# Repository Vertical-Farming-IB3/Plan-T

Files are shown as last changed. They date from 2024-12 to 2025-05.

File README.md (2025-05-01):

# Plan-T 🌱  

Plan-T is een vertical farming (VF) project met hydroponics, gericht op het duurzaam kweken van kruiden en groenten. De VF-installatie wordt grotendeels automatisch bestuurd en gemonitord, met ruimte voor menselijke input waar nodig — zoals bij controle, onderhoud en oogst (een vorm van mens-in-de-lus automatisering).

## Voor meer info:  
- [Team Plantenbak](./Plantenbak)  
- [Team Water](./Water)  
- [Team Licht](./Licht)
- [Team Power](./Power)  

Bezoek onze [website](https://vertical-farming-ib3.github.io/),
en zijn [repository](https://github.com/Vertical-Farming-IB3/vertical-farming-ib3.github.io/tree/main).

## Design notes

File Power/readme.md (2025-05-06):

Meer info [hier](https://vertical-farming-ib3.github.io/Power/).

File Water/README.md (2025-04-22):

# Water 💧

Onze groep bestaat uit:
- Charlotte Bert
- Kjell Naessens
- Niels Verhoeve
- Sander Haustraete

Wij verzorgen het watersysteem en alles dat daarmee te maken heeft! Onze PCB bestuurt de pompjes, mixers, UV-filter, ... en leest waarden in van hoogtesensoren, chemische probes, ...

Voor een volledige beschrijving van het watersysteem kan je terecht op [onze webpagina](https://vertical-farming-ib3.github.io/Water/).

Meer documentatie over de PCB vind je [hier](./PCB/), meer documentatie over de chemische probes [hier](./Chemische_probes.md) en meer documentatie over de vermogensmeting [hier](./Vermogensmeting.md).

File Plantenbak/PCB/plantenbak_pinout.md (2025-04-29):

## Onboard led: 
- GPIO2

## Fans:
- GPIO32 ( relais )
- 12V power

## NFC:
- I²C:
  - SDA op GPIO21
  - SCL op GPIO22
- VCC (3.3V)
- GND
  
## GY-SCD4:
- I²C: GPIO21 en 22
- VCC (3.3V)
- GND
  
## Capacitive soil moisture sensor
- GPIO34
- VCC (3.3V)
- GND
  
## Stroommeter
- GPIO35
- VCC (3.3V)
- GND

## BH1750 lichtmeter
- I²C: GPIO21 en 22
- VCC (3.3V)
- GND
- PULL DOWN

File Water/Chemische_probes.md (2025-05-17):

# Probes en hun belangrijkste kenmerken

## 232-01 Referentie-Elektrode Glazen Schaal Enkele Zoutbrug Referentiesonde Sensor:
Link: [232-01 Referentie-elektrode Glazen Schaal Enkele Zoutbrug Referentiesonde Sensor - Buy Reference Electrode Product on Alibaba.com](https://www.alibaba.com/product-detail/232-01-Reference-Electrode-Glass-Shell_60668853882.html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)

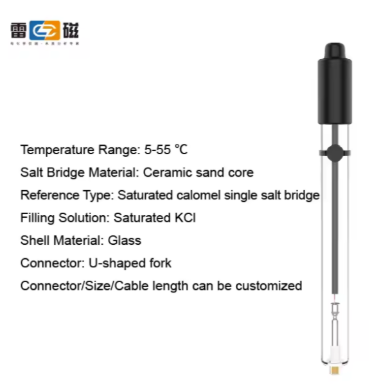
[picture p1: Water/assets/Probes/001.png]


### Belangrijkste kenmerken
#### Andere specificaties

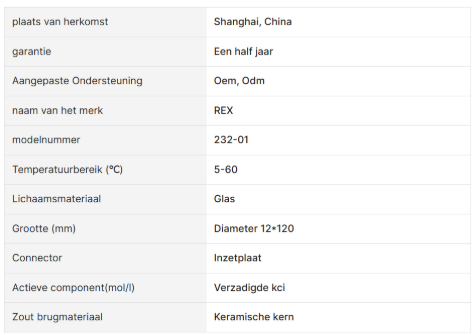
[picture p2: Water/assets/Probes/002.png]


## PCa-1-01 Calciumion Selectieve Sonde Isode Ca + Sensor
Link: [Pca-1-01 Calciumion Selectieve Sonde Isode Ca + Sensor - Buy Ion Selective Probe,Calcium Ion Selective Probe,Ion Selective Probe Product on Alibaba.com](https://www.alibaba.com/product-detail/PCa-1-01-Calcium-Ion-Selective_60659669573.html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)

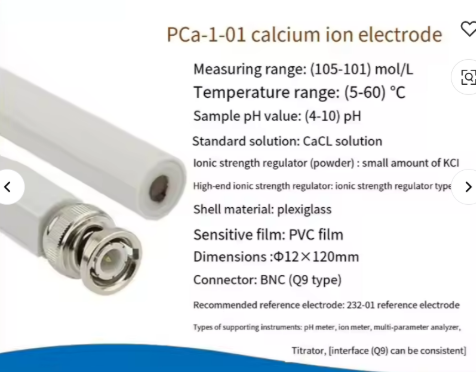
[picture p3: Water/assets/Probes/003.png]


### Belangrijkste kenmerken
#### Andere specificaties

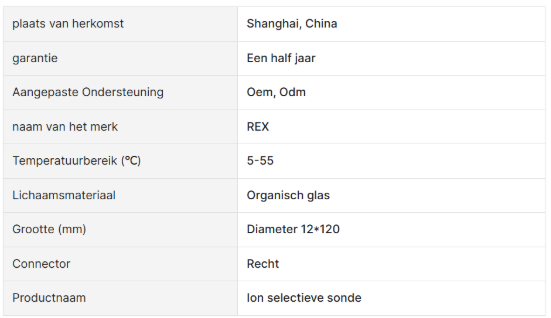
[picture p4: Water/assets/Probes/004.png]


## Ise K + Kalium Ion Selectieve Elektrode Bnc Connector Laboratorium En Gebruik Voor Waterkwaliteit Detectie Kalium Test Px Meter

Link: [Ise K + Kalium Ion Selectieve Elektrode Bnc Connector Laboratorium En Gebruik Voor Waterkwaliteit Detectie Kalium Test Px Meter - Buy Potassium ion Selective electrode Product on Alibaba.com](https://www.alibaba.com/product-detail/ISE-K-Potassium-Ion-Selective-Electrode_1600225607843.html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)

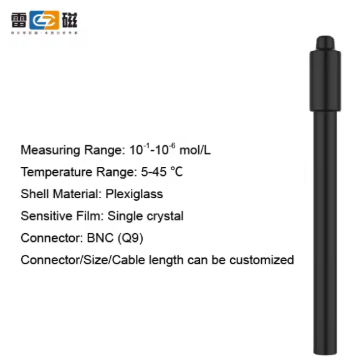
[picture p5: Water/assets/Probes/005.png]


### Belangrijkste kenmerken
#### Andere specificaties

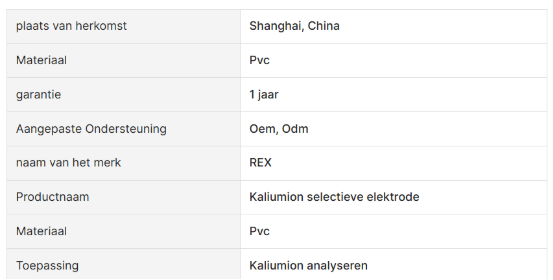
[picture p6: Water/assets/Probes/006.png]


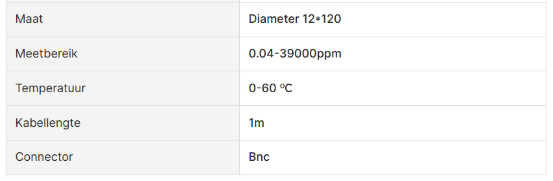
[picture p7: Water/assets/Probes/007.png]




## Nitraat Ion-Selectieve Elektrode No3-Ise Sonde Nitraat Ionen Verbindingen Algemene Water Test Bnc Connector

Link: [Nitraat Ion-selectieve Elektrode No3-ise Sonde Nitraat Ionen Verbindingen Algemene Water Test Bnc Connector - Buy Ion-selective Electrode no3- Ise Probe nitrate Ions Compounds Product on Alibaba.com](https://www.alibaba.com/product-detail/Nitrate-Ion-selective-Electrode-NO3-ISE_60817798149.html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)

### Belangrijkste kenmerken
#### Andere specificaties

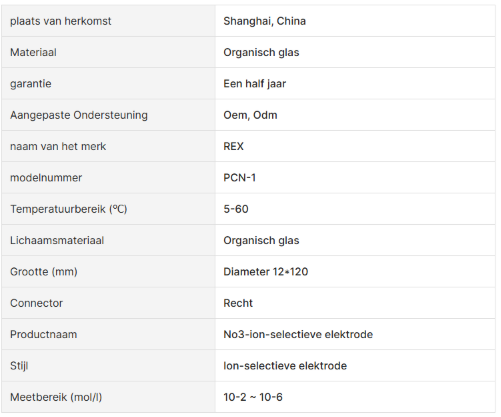
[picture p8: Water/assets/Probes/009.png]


Nauwkeurigheid: 0.01

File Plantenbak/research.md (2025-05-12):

---

## Research en vergelijking van sensoren

In deze sectie vergelijken we enkele van onze gekozen sensoren met alternatieve opties, op basis van nauwkeurigheid, prijs, beschikbaarheid, duurzaamheid en gebruiksgemak. Op basis van deze vergelijkingen motiveren we ook telkens onze keuze.

---

### Luchtsensor (GY-SCD40)

#### Vergelijking met alternatieven:

| Sensor | Parameters | Voeding | Interface | Nauwkeurigheid | Prijsindicatie | Opmerkingen |
|---|---|---|---|---|---|---|
| GY-SCD40 | CO₂, temperatuur, vochtigheid| 3.3V/5V | I²C | Hoog | Hoog | Compact, snel, nauwkeurig |
| MH-Z19B | CO₂ | 5V | UART | Matig | Gemiddeld | Alleen CO₂, trager, minder stabiel |
| CCS811 | eCO₂, TVOC | 3.3V | I²C | Laag tot gemiddeld | Laag | Indirecte CO₂, inferieur aan GY-SCD40 |

Zie onderstaande links voor verschillende sensoren:
- [GY-SCD40](https://www.tinytronics.nl/nl/sensoren/lucht/vochtigheid/gy-scd40-module-co2-luchtvochtigheid-en-temperatuursensor-i2c)
- [MH-Z19B](https://www.tinytronics.nl/nl/winsen-mh-z19b-co2-sensor-met-kabel)
- [CCS811](https://www.adafruit.com/product/3566)

#### Voordelen:
- Hoge nauwkeurigheid  
- Meet drie parameters tegelijk  
- Compact en efficiënt  

#### Nadelen:
- Duurder  
- Heeft enkele seconden opwarmtijd nodig  

**Keuze-motivatie:** Ondanks de hogere kostprijs is de SCD40 superieur door de combinatie van nauwkeurigheid, snelheid en veelzijdigheid. Dankzij hergebruik van een vorig project was er bovendien geen extra kost.

---

### NFC-lezer (PN532)

#### Vergelijking met alternatieven:

| Sensor | Interface | Bereik | Compatibiliteit | Prijsindicatie | Opmerkingen |
|---|---|---|---|---|---|
| PN532 | I²C/SPI/UART  | ~3 cm  | ISO/IEC 14443 A/B | Gemiddeld | Veelgebruikt, goede bibliotheekondersteuning |
| RC522 | SPI | ~2 cm  | ISO/IEC 14443 A | Laag | Korter bereik, minder robuust |
| MFRC630 | SPI/I²C | ~5 cm  | 14443 A/B + NFC Forum  | Hoog | Sneller en flexibeler, maar duurder en minder ingeburgerd |

Zie onderstaande links voor verschillende sensoren:
- [PN532](https://www.tinytronics.nl/en/communication-and-signals/wireless/rfid/rfid-nfc-kit-pn532-with-s50-card-and-s50-key-tag)
- [RC522](https://www.tinytronics.nl/nl/communicatie-en-signalen/draadloos/rfid/rfid-kit-mfrc522-s50-mifare-met-kaart-en-key-tag)
- [MFRC630](https://gr.mouser.com/c/semiconductors/wireless-rf-integrated-circuits/nfc-rfid-tags-transponders/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)
  
#### Voordelen:
- Brede ondersteuning, meerdere protocollen  
- Betrouwbaar en compatibel met ESP  
- Goede bibliotheekondersteuning  

#### Nadelen:
- Duurder dan RC522  
- Groter formaat  

**Keuze-motivatie:** De PN532 was beschikbaar op de campus en heeft een goede compatibiliteit met ESP32 en ESPHome. Daardoor was het de beste keuze voor snelle implementatie.

---

### Energiemonitoring (ACS712)

#### Vergelijking met alternatieven:

| Sensor | Meetprincipe | Meetbereik | Interface | Nauwkeurigheid | Prijsindicatie | Opmerkingen |
|---|---|---|---|---|---|---|
| ACS712 | Hall-effect | ±5A/20A/30A| Analoog | Gemiddeld | Laag | Beperkte resolutie, gevoelig aan ruis |
| INA219 | Shunt + ADC | Tot 3.2A | I²C | Hoog | Gemiddeld | Beter voor lage stromen, nauwkeuriger |
| SCT-013 | Transformatorspoel| 100A | Analoog | Laag tot gemiddeld | Laag | Alleen AC, extra burden resistor nodig |

Zie onderstaande links voor verschillende sensoren:
- [ACS712](https://www.tinytronics.nl/nl/sensoren/stroom-spanning/acs712-stroomsensor-module-20a)
- [INA219](https://www.tinytronics.nl/en/sensors/current-voltage/ina219-i2c-dc-current-and-voltage-meter-3.2a-module)
- [SCT-013](https://www.tinytronics.nl/nl/sensoren/stroom-spanning/ac-stroom-sensor-sct013-030-30a)

#### Voordelen:
- Simpel aan te sluiten (analoog)  
- Meet zowel AC als DC  
- Goedkoop en goed beschikbaar  

#### Nadelen:
- Gevoelig voor ruis  
- Lage resolutie, niet geschikt voor hele kleine stromen  

**Keuze-motivatie:** Omdat het systeem op lage stroom werkt, was de ACS712 accuraat genoeg voor onze noden. Bovendien had een teamlid deze sensor al thuis liggen, waardoor we dus budget konden sparen.

---

### Bodemsensor (Capacitive Soil Sensor v2)

#### Vergelijking met alternatieven:

| Sensor | Meetprincipe | Interface | Waterbestendig | Levensduur | Prijsindicatie | Opmerkingen |
|---|---|---|---|---|---|---|
| Capacitive Soil Sensor v2 | Capacitatief | Analoog | Spatwaterdicht | Gemiddeld  | Laag | Goede optie voor hydroponics |
| Resistive sensor (YL-69)  | Weerstandsmeting | Analoog | Nee | Laag | Zeer laag | Roest snel, onnauwkeurig |
| DFRobot SEN0193 | Capacitief digitaal  | UART/I2C/analog  | Waterdicht | Zeer goed  | Hoog (± €25–€35)| Professionele sensor, waterdicht, nauwkeurig |

Zie onderstaande links voor verschillende sensoren:
- [v2](https://www.tinytronics.nl/en/sensors/liquid/capacitive-soil-moisture-sensor-module-with-cable)
- [YL-69](https://nl.aliexpress.com/item/1005004305871722.html)
- [DFRobot SEN0193](https://be.farnell.com/dfrobot/sen0193/analog-capacitive-soil-moisture/dp/2946124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)

#### Voordelen:
- Capacitatieve meting is nauwkeuriger dan resistieve  
- Redelijk bestand tegen vocht  
- Werkt goed met ESPHome  

#### Nadelen:
- Niet volledig waterdicht  
- Niet geschikt voor diepe grondlagen  

**Keuze-motivatie:** Voor hydroponics volstaat een gemiddelde nauwkeurigheid. Deze sensor was reeds aanwezig in de klas en biedt een goed evenwicht tussen betrouwbaarheid en kost.

---

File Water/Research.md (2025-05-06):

# Research Water 
## Ontsmetten van mixreservoir 
Heel wat oplossingen voor het ontsmetten/zuiveren van het mixreservoir is duur en niet meteen beschikbaar.

Een zandfilter is een effectief systeem, maar moet regelmatig vervangen worden en brengt mogelijks hoge onderhoudskosten met zich mee.

Het gebruik van UV-C lampen, is effectief, onderhoudsvriendelijk en heeft een levensduur van 8000 uur wat goed is voor onze toepassing. Voor een effectieve werking mikken we op een golflengte tussen de 254 en 265 nm.

Voor de UV-C ontsmetting zijn er drie mogelijke plaatsingen besproken:

1. Boven alle reservoirs
  - Voordeel: Eén lamp kan meerdere reservoirs ontsmetten.
  - Nadeel: Grotere afstand en minder afscherming zorgen voor lagere effectiviteit en verhoogd risico op blootstelling van mens en dier aan schadelijk licht. Ook zou dit de levensduur van de tubes verlagen.

2. In het mengreservoir
  - Voordeel: Direct contact met het meest besmette water.
  - Nadeel: Enkel het mengreservoir wordt gezuiverd, en er is geen interne reflectie die de effectiviteit verhoogt.

3. Extern via tubes
  - Voordeel: Veelzijdig inzetbaar met pompsystemen en maakt gebruik van interne reflectie, wat zorgt voor een efficiëntere werking.
  - Nadeel: Meer externe hardware en coördinatie nodig, wat de kosten verhoogt.

Bij de keuze van de lamp houden we rekening met het benodigde vermogen, gebaseerd op het volume van de reservoirs en de concentratie voedingsstoffen. We streven naar een vermogen van ongeveer 10 watt.
Wij hebben gekozen voor optie 2, in het mengreservoir. Dit was het beste te implementeren in ons systeem. 

Ten slotte wensen we de lamp aan te sturen via een PCB met ESPHome, gekoppeld aan Home Assistant. Hiervoor kiezen we bewust voor een eenvoudige lamp zonder ingebouwde timer, die via een relais en schakelaar kan worden bestuurd.

De eerst bestelde UVC-lamp via AliExpress gaf problemen: deze ontplofte al na zeven minuten gebruik. Dit onderstreept het belang van kwaliteitsvolle componenten en betrouwbare leveranciers.

## Waterniveau Sensor

Er zijn verschillende opties voor waterniveau meting:

| Kenmerk | Waterniveau Sensor | DFRobot Contactloze Sensor | Ultrasone Sensor |
|---|---|---|---|
| Meetprincipe | Weerstand (direct contact) | Capacitief (contactloos) | Ultrasoon geluid |
| Contactloos? | Nee | Ja | Ja |
| Output | Analoog | Digitaal | Analoog |
| Meetbereik | Verschillende niveaus | Alleen "aan/uit" detectie | 2-450 cm |
| Nauwkeurigheid | Afhankelijk van vloeistofconductiviteit en corrosie | Betrouwbaar, maar geen niveau-indicatie | 3mm |
| Geschikt voor alle vloeistoffen? | Nee, alleen geleidende vloeistoffen | Ja | Ja |
| Corrosiegevoelig? | Ja | Nee | Nee |
| Prijs | Goedkoop | Duurder | 1-3 euro |
| Toepassing | Waterniveau meten | Vloeistofniveau detecteren zonder contact | Zeer nauwkeurig vloeistofniveau opmeten |

Zie onderstaande links voor verschillende sensoren:
- [Waterniveau Sensor](https://www.tinytronics.nl/nl/sensoren/vloeistof/waterniveau-sensor)
- [DFRobot Contactloze Sensor](https://www.tinytronics.nl/nl/sensoren/vloeistof/dfrobot-gravity-contactloze-vloeistofniveau-schakelaar-sensor)
- [Ultrasone Sensor](https://www.tinytronics.nl/en/sensors/distance/ultrasonic-sensor-hc-sr04)

We kozen voor de ultrasone sensor. De waterniveausensor was ook een goede keuze maar leek ons toch net niet helemaal geschikt. Beiden hebben nadelen en voordelen.

## Mixer
Er zijn verschillende opties voor watercirculatie:

- *Aquariumpomp*  
  - Voordelen: Sterke circulatie  
  - Nadelen: turbulentie veroorzaken en kan verstopt geraken  

- *Luchtpomp + luchtsteen*  
  - Voordelen: Zachte menging, weinig energieverbruik  
  - Nadelen: Trage menging en schuimvorming  

- *Mechanische mixer*  
  - Voordelen: Efficiënt mengen zonder veel turbulentie  
  - Nadelen: Mechanisch => onderhoud nodig  

We kozen voor een luchtpompje bij de reservoirs beneden. Dankzij een luchtsteen zal het water voldoende gecirculeerd worden.

Voor het reservoir kozen we een aquariumpompje. Dit heeft niet veel water nodig om een voldoende turbulente stroom te voorzien die het water mengt. Dit pompje sturen we aan op basis van de hoogte in dit bovenste reservoir.

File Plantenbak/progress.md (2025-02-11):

# Plantenbak
Teamleden:
  - Beau Forrez
  - Elias Neels
  - Wout Batselé
  - ...
  - ...

## To-do lijst
- [ ] Componentenlijst opstellen

## In Progress
- [ ] Componenten van vorig jaar testen en proberen te hergebruiken
- [ ] De server terug werkende krijgen

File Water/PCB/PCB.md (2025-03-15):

# PCB Watersysteem

In dit document sommen we de requirements op voor de PCB.

## Inputs
- Analoog (x3) voedingstoffen => via 1 ADC (ADS1115) met BNC connectoren voor de probes
- Analoog (x3) Ultrasone hoogtesensoren (HC-SR04)
- Digitaal (x3) eindeloopschakelaars

## Outputs
- Digitaal LED indicator waterniveau
- Digitaal LED indicator voedingsstofniveau
- Relais UV lamp (230V/100mA)
- Relais mixer pompje (3V/200mA) of (6V/200mA)
- Relais pompjes lade en reservoirs (4x) (12V/400mA)
- Relais luchtpomp (12V/220mA)

# Power inputs

12V DC / 3A

230V AC / 100mA

Dit wordt op de PCB door een buck converter (MP1584) van 12V naar 5V omgezet voor de relais. De 5V wordt verder omgevormd naar 3.3V door een LDO (AMS1117) voor de ESP32.
## Vermogen 12V
- 4x pompje van 400mA
- 1x luchtpomp 220mA
- 1x mixer pompje 100mA
- relais (200mA bij 5V) => 100mA
- Buck converter (1500mA bij 5V) => 800mA

Afgerond maakt dit 3000mA bij 12V \
=> P = 40W

# Pinout
Nummers: ESP32

A/B: IO expander \
IO expander is met I2C verbonden met de ESP32

### LEDs
Pin| Description
---|------------
2  | Onboard LED (IO2)
A7 | Water LED
B0 | Nutriënten LED

### Hoogtesensoren (ultrasoon)
Pin| Description
---|------------
26 | Trigger Hoogtesensor Nutr
25 | Echo Hoogtesensor Nutr
33 | Trigger Hoogtesensor Water
32 | Echo Hoogtesensor Water
14 | Trigger Hoogtesensor Mix
27 | Echo Hoogtesensor Mix

### Eindeloopschakelaars
Normaal open

Open = Hoog, Gesloten = Laag

 Pin | Description
-----|------------
 B1  | Schakelaar 1
 B2  | Schakelaar 2
 B3  | Schakelaar 3

### Relais

 Pin | Description
-----|------------
 A0  | Mixer
 A1  | UV lamp
 A2  | Luchtpomp
 A3  | Pomp 4
 A4  | Pomp 3
 A5  | Pomp 2
 A6  | Pomp 1

### Backup IO

Pin| Description
---|------------
B4 | B4
B5 | B5
B6 | B6
B7 | B7

### IO expander
I2C adres: 0X27

Het adres is herinstelbaar via JP1, JP2 en JP3 (verbind de jumpers voor een 0, ze zijn standaard 1): \
0b0100\<JP1>\<JP2>\<JP3>

### ADC en probes
I2C adres: 0x48 \
Verbind JP4 voor adres 0x49

Pin| Description
---|------------
A0 | Nutriënten 3
A1 | Nutriënten 2
A2 | Nutriënten 1
A3 | Referentie

Testpunten zijn aangeduid op de PCB

### I2C

Pin| Description
---|------------
17 | SCL
18 | SDA

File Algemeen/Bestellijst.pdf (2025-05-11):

Component | Status | Link | Aantal/module plantenbak | Aantal/module kast | Aantal in bezit | Totaal aantal | Totaal aantal te bestellen | Prijs/eenheid Kost | Prijs | Info | Totaal Watersysteem (Te bestellen) | Aantal modules kast:
WATERSYSTEEM | € 123,39 | 1
Waterpomp (12VDC) | In bezit | TinyTronics | 4 | 4 | 4 | € 6,00 | 24,00 € | 24,00 € | Aantal modules plantenbak per module kast:
Aquariumpomp (mengen) | In bezit | TinyTronics | 1 | 1 | 1 | € 4,00 | 4,00 € | 4,00 € | 2
Sensor ISE-2922 NO3- | In bezit | MTLAB | 1 | 1 | 1 | 0 | € 36,83 | 36,83 € | - € | Totaal aantal modules plantenbak:
Sensor ISE-2923 Ca2+ | In bezit | MTLAB | 1 | 1 | 1 | 0 | € 27,62 | 27,62 € | - € | 2
Sensor ISE-2920 K+ | In bezit | MTLAB | 1 | 1 | 1 | 0 | € 32,22 | 32,22 € | - €
ADC | In bezit | 1 | 1 | 1 | 0 | € 0,00 | - € | - € | op pcb
UV | Kapot | Aliexpress | 1 | 1 | 1 | € 10,43 | 10,43 € | 10,43 € | TOTALE KOST: | Excl verzending, excl xtra kosten, incl btw
Waterhoogte sensor: Ultrasoon | In bezit | TinyTronics | 3 | 3 | 3 | 0 | € 2,75 | 8,25 € | - €
QuickConnects water | In bezit | Aliexpress | 2 | 4 | 4 | 1 | € 0,97 | 3,88 € | 0,97 € | PU-8 voor 8 mm OD (1x 10 stuks bestellen) | TOTAAL TE BESTELLEN:
Waterslang (6mm ID-8mm OD) | In bezit | TinyTronics | 6 | 6 | 6 | € 1,50 | 9,00 € | 9,00 € | per meter (AAN 1 STUK BESTELLEN!) | € 766,62
Silicone kit | In bezit | Hubo | 1 | 1 | 1 | 0 | € 6,50 | 6,50 € | - €
Klemringen/Slangklemmen | In bezit | Aliexpress | 1 | 1 | 1 | € 2,33 | 2,33 € | 2,33 € | Per 10
Reservoir | In bezit | Vorig jaar | 4 | 4 | 4 | 0 | € 2,99 | 11,96 € | - €
Luchtsteen | In bezit | Aliexpress | 2 | 2 | 2 | € 0,97 | 1,94 € | 1,94 €
T stuk (luchtsteen) | In bezit | Aliexpress | 1 | 1 | 1 | € 0,97 | 0,97 € | 0,97 €
Luchtpomp | In bezit | TinyTronics | 2 | 2 | 2 | € 4,50 | 9,00 € | 9,00 €
Waterslang (3.5mm ID-Xmm OD) | In bezit | TinyTronics | 1 | 1 | 1 | € 2,00 | 2,00 € | 2,00 € | per meter, 3.5mm
Eindeloopschakelaars | In bezit | Hobbyelectronica | 3 | 3 | 3 | 0 | € 1,95 | 5,85 € | - €
PCBs | In bezit | PCBWay | 1 | 1 | 1 | € 4,39 | 4,39 € | 4,39 €
Relais 5V | In bezit | Mouser | 10 | 10 | 10 | € 1,47 | 14,70 € | 14,70 €
waterslang | In bezit | tinytronics | 1 | 1 | 1 | € 1,50 | € 1,50 | 1,50 €
PPF | In bezit | AliExpress | 5 | 5 | 5 | € 0,75 | € 3,80 | 3,80 €
PH- sensor + ADC | In bezit | AliExpress | 1 | 1 | € 4,52 | € 4,52 | 4,52 €
UV-C filter (nieuw) [14W - ordinary] | In bezit | AliExpress | 1 | 1 | € 29,84 | € 29,84 | 29,84 €
Componenten PCB
Footprint | Value | References | | | | | | | | Aanwezig op campus
C_0805_2012Metric_Pad1.18x1.45mm_HandSolder | 100n | C3, C4, C6, C7, C10, C11, C12, C13, C14 | 9 | 9 | 9 | 0 - | - | -
CP_Elec_6.3x3.9 | 100u | C1, C2 | 2 | 2 | 2 | 0 - | - | -
C_0805_2012Metric_Pad1.18x1.45mm_HandSolder | 10u | C5, C9 | 2 | 2 | 2 | 0 - | - | -
CP_EIA-3528-12_Kemet-T_Pad1.50x2.35mm_HandSolder | 22u | C8 | 1 yyyyy | 1 | 0 - | - | -
R_0805_2012Metric_Pad1.20x1.40mm_HandSolder | 10k | R2, R4, R5, R6, R7, R8, R9, R11, R13 | 9 | 9 | 9 | 0 - | - | -
R_0805_2012Metric_Pad1.20x1.40mm_HandSolder | 470 | R1, R3, R14, R15 | 4 | 4 | 4 | 0 - | - | -
R_0805_2012Metric_Pad1.20x1.40mm_HandSolder | 4.7k | R10, R12 | 2 | 2 | 2 | 0 - | - | -
D_0805_2012Metric_Pad1.15x1.40mm_HandSolder | 1N4148 | D4, D5, D6, D7, D8, D9, D10 | 7 | 7 | 7 | 0 - | - | -
LED_0805_2012Metric_Pad1.15x1.40mm_HandSolder | PWR | D1 | 1 | 1 | 1 | 0 - | - | -
LED_0805_2012Metric_Pad1.15x1.40mm_HandSolder | LED | D2 | 1 | 1 | 1 | 0 - | - | -
DIOM5226X290N | SK36A | D3 | 1 | 1 | 1 | 0 - | - | -
MP1584_Module | MP1584_Module | U1 | 1 | 1 | 1 | 0 - | - | -
ESP32-WROOM-32D | ESP32-WROOM-32D | U2 | 1 | 1 | 1 | 0 - | - | -
TSSOP-10_3x3mm_P0.5mm | ADS1115IDGS | U3 | 1 | 1 | 1 | 0 - | - | -
SOT-223-3_TabPin2 | AMS1117-3.3 | U4 | 1 | 1 | 1 | 0 - | - | -
SOIC-28W_7.5x17.9mm_P1.27mm | MCP23017_SO | U5 | 1 | 1 | 1 | 0 - | - | -
Wurth_Tactile_Switch_SPST-NO_434111043826 | EN | SW1 | 1 | 1 | 1 | 0 - | - | -
Wurth_Tactile_Switch_SPST-NO_434111043826 | BOOT | SW2 | 1 | 1 | 1 | 0 - | - | -
AHQSS105DM2FA0G | AHQSS105DM2FA0G | K1, K2, K3, K4, K5, K6, K7 | 7 | 7 | 7 | 0 - | - | -
SOT-23 | BSS138 | Q1, Q2, Q3, Q4, Q5, Q6, Q7 | 7 | 7 | 7 | 0 - | - | -
MountingHole_3.2mm_M3_Pad_TopBottom | MountingHole_Pad | H1, H2, H3, H4 | 4 | 4 | 4 | 0 - | - | -
SolderJumper-2_P1.3mm_Open_RoundedPad1.0x1.5mm | SolderJumper_2_Open | JP1, JP2, JP3, JP4 | 4 | 4 | 4 | 0 - | - | -
TestPoint_Pad_D2.0mm | TestPoint | TP1, TP2, TP3, TP4 | 4 | 4 | 4 | 0 - | - | -
PinHeader_1x04_P2.54mm_Vertical | Height Water | J1 | 1 | 1 | 1 | 0 - | - | -
PinHeader_1x04_P2.54mm_Vertical | Height Nutrients | J2 | 1 | 1 | 1 | 0 - | - | -
PinHeader_1x04_P2.54mm_Vertical | Height Mixer | J3 | 1 | 1 | 1 | 0 - | - | -
PinHeader_1x02_P2.54mm_Vertical | TestPins | J4 | 1 | 1 | 1 | 0 - | - | -
TerminalBlock_Phoenix_PT-1,5-2-5.0-H_1x02_P5.00mm_Horizontal | 12V ingang | J5 | 1 | 1 | 1 | 0 - | - | -
TerminalBlock_Phoenix_PT-1,5-2-5.0-H_1x02_P5.00mm_Horizontal | Pomp1 | J6 | 1 | 1 | 1 | 0 - | - | -
PinHeader_1x04_P2.54mm_Vertical | TTL Connector | J7 | 1 | 1 | 1 | 0 - | - | -
PinHeader_1x03_P2.54mm_Vertical | Endstop UV | J8 | 1 | 1 | 1 | 0 - | - | -
PinHeader_1x03_P2.54mm_Vertical | Endstop Lade1 | J9 | 1 | 1 | 1 | 0 - | - | -
BNC_Amphenol_B6252HB-NPP3G-50_Horizontal | ReferentieProbe | J10 | 1 | 1 | 1 | 0 - | - | -
PinHeader_1x03_P2.54mm_Vertical | Endstop Lade0 | J11 | 1 | 1 | 1 | 0 - | - | -
TerminalBlock_Phoenix_PT-1,5-2-5.0-H_1x02_P5.00mm_Horizontal | Pomp2 | J12 | 1 | 1 | 1 | 0 - | - | -
PinHeader_1x02_P2.54mm_Vertical | LED Water Level | J13 | 1 | 1 | 1 | 0 - | - | -
PinHeader_1x02_P2.54mm_Vertical | LED Nutrient Level | J14 | 1 | 1 | 1 | 0 - | - | -
BNC_Amphenol_B6252HB-NPP3G-50_Horizontal | Voedingsstoffen 1 | J15 | 1 | 1 | 1 | 0 - | - | -
TerminalBlock_Phoenix_PT-1,5-2-5.0-H_1x02_P5.00mm_Horizontal | Pomp3 | J16 | 1 | 1 | 1 | 0 - | - | -
TerminalBlock_Phoenix_PT-1,5-2-5.0-H_1x02_P5.00mm_Horizontal | Pomp4 | J17 | 1 | 1 | 1 | 0 - | - | -
PinHeader_1x06_P2.54mm_Vertical | Backup GPIO | J18 | 1 | 1 | 1 | 0 - | - | -
BNC_Amphenol_B6252HB-NPP3G-50_Horizontal | Voedingsstoffen 2 | J19 | 1 | 1 | 1 | 0 - | - | -
TerminalBlock_Phoenix_PT-1,5-2-5.0-H_1x02_P5.00mm_Horizontal | Luchtpomp | J20 | 1 | 1 | 1 | 0 - | - | -
BNC_Amphenol_B6252HB-NPP3G-50_Horizontal | Voedingsstoffen 3 | J21 | 1 | 1 | 1 | 0 - | - | -
TerminalBlock_Phoenix_PT-1,5-2-5.0-H_1x02_P5.00mm_Horizontal | Mixer | J22 | 1 | 1 | 1 | 0 - | - | -
TerminalBlock_Phoenix_PT-1,5-2-5.0-H_1x02_P5.00mm_Horizontal | 230V | J23 | 1 | 1 | 1 | 0 - | - | -
TerminalBlock_Phoenix_PT-1,5-2-5.0-H_1x02_P5.00mm_Horizontal | UV | J24 | 1 | 1 | 1 | 0 - | - | -
PLANTENBAK | | | | | | | | | | | Totaal Plantenbak (Te bestellen)
Capacitive soil moisture sensor | In bezit | 1 | 2 | 2 | 2 | € 87,43
GY-SCD40 module | In bezit | 1 | 2 | 2 | 2
NFC-reader PN532 | In bezit | 1 | 2 | 2 | 2
NFC-tags | In bezit | 1 | 2 | 2 | 2
Nieuwe PCB's | In bezit | PCBWay | 1 | 2 | 2 | 2 | 4,39 €
BH1750 lichtsensor | In bezit | Hobbyelectronica | 1 | 2 | 2 | 2 | € 2,25 | € 4,50 | 4,50 €
CH340C | In bezit | AliExpress | 1 | 2 | 10 | 10 | € 0,41 | € 4,05 | 4,05 €
ESP-WROOM-32 | In bezit
Ventilatoren (12V) | In bezit | 2 | 4 | 4 | 4
Relais SR5 | In bezit | Digikey | 1 | 2 | 2 | 2 | € 1,13 | € 2,26 | 2,26 €
MP1584 | In bezit | TinyTronics | 1 | 2 | 2 | 2 | € 1,50 | € 3,00 | 3,00 €
Dupont kabels | In bezit | 4 | 4 | € 2,00 | € 8,00 | 8,00 €
5V relais | In bezit | Tinytronics | 2 | 2 | € 2,50 | € 5,00 | 5,00 €
rockwol aliexpress | In bezit | AliExpress | 1 | 1 | € 4,65 | € 4,65 | 4,65 € | 100 stuks per batch
potjes voor plantjes: NO.40 white | In bezit | AliExpress | 2 | 2 | € 3,28 | € 3,28 | 6,56 € | NO.50 white (15 stuk per batch)
witte verf | In bezit | Action | 1 | 1 | € 7,99 | € 7,99 | 7,99 €
verfborstel en verfbak | In bezit | action | 1 | 1 | € 1,84 | € 1,84 | 1,84 €
kokosvezel potgrond | In bezit | Action | 3 | 3 | € 1,17 | € 3,51 | 3,51 €
plantenvoeding | In bezit | Action | 2 | 2 | € 1,79 | € 3,58 | 3,58 €
bloempotjes | In bezit | action | 2 | 2 | € 1,11 | € 2,22 | 2,22 €
hydrokorrels | In bezit | Action | 1 | 1 | € 2,37 | € 2,37 | 2,37 €
Glasbokalen | In bezit | Action | 9 | 9 | € 0,89 | € 8,01 | 8,01 €
Kitlijm voor bakken | In bezit | Gamma | 1 | 1 | € 11,00 | € 11,00 | 11,00 €
Regentonkraan voor bakken | In bezit | EuroShop | 1 | 1 | € 4,50 | € 4,50 | 4,50 €
Componenten PCB
Footprint | Value | References | | | | | | | | Aanwezig op campus
Capacitor_SMD:C_0805_2012Metric_Pad1.18x1.45mm_HandSolder | 10u | C1 C7 C8 C9 C12 | 5 | 10 | 10 | 10 | 0
Capacitor_SMD:C_0805_2012Metric_Pad1.18x1.45mm_HandSolder | 100n | C2 C3 C10 C11 | 4 | 8 | 8 | 8 | 0
Capacitor_SMD:C_0805_2012Metric_Pad1.18x1.45mm_HandSolder | 1u | C5 | 1 | 2 | 2 | 2 | 0
Capacitor_SMD:C_0805_2012Metric_Pad1.18x1.45mm_HandSolder | 100u | C6 | 1 | 2 | 2 | 2 | 0
Diode_SMD:D_SOD-323_HandSoldering | D_Schottky | D1 D4 | 2 | 4 | 4 | 4 | 0
LED_SMD:LED_0805_2012Metric_Pad1.15x1.40mm_HandSolder | LED | D2 D3 | 2 | 4 | 4 | 4 | 0
Diode_SMD:D_SOD-123 | 1N4148W | D5 | 1 | 2 | 2 | 2 | 0
Connector_PinHeader_2.54mm:PinHeader_1x02_P2.54mm_Vertical | Conn_01x02 | J2 J3 | 2 | 4 | 4 | 4 | 0
Connector_PinHeader_2.54mm:PinHeader_1x04_P2.54mm_Vertical | Conn_01x04 | J4 J8 J14 J15 | 4 | 8 | 8 | 8 | 0
Connector_PinHeader_2.54mm:PinHeader_1x05_P2.54mm_Vertical | Conn_01x05 | J5 J7 | 2 | 4 | 4 | 4 | 0
Connector_PinHeader_2.54mm:PinHeader_1x10_P2.54mm_Vertical | Conn_01x10 | J6 J10 | 2 | 4 | 4 | 4 | 0
TerminalBlock_Phoenix:TerminalBlock_Phoenix_MKDS-1 | Screw_Terminal_01x02 | J9 J11 | 2 | 4 | 4 | 4 | 0
Connector_PinHeader_2.54mm:PinHeader_2x02_P2.54mm_Vertical | Conn_02x02_Counter_Clockwise J12 | 1 | 2 | 2 | 2 | 0
Connector_PinHeader_2.54mm:PinHeader_1x03_P2.54mm_Vertical | Conn_01x03 | J13 | 1 | 2 | 2 | 2 | 0
Package_TO_SOT_SMD:SOT-23 | BSS138 | Q1 Q2 Q3 Q4 Q5 | 5 | 10 | 10 | 10 | 0
Resistor_SMD:R_0805_2012Metric_Pad1.20x1.40mm_HandSolder | 4K7 | R1 R2 R5 R6 | 4 | 8 | 8 | 8 | 0
Resistor_SMD:R_0805_2012Metric_Pad1.20x1.40mm_HandSolder | 1M | R3 | 1 | 2 | 2 | 2 | 0
Resistor_SMD:R_0805_2012Metric_Pad1.20x1.40mm_HandSolder | 10K | R4 R7 R8 R9 R10 R11 R12 R14 R16 | 9 | 18 | 18 | 18 | 0
Resistor_SMD:R_0805_2012Metric_Pad1.20x1.40mm_HandSolder | 1K | R13 R15 R17 | 3 | 6 | 6 | 6 | 0
434111043826:434111043826 | SW_Push | SW1 SW2 | 2 | 4 | 4 | 4 | 0
Watersysteem_Footprints_Library:MP1584_Module | MP1584_Module | U1 | 1 | 2 | 2 | 2 | 0
Package_TO_SOT_SMD:SOT-223-3_TabPin2 | AMS1117-3.3 | U2 | 1 | 2 | 2 | 2 | 0
RF_Module:ESP32-WROOM-32E | ESP32-WROOM-32E | U4 | 1 | 2 | 2 | 2 | 0
Verlichting en power | nt | | | | | | | | | | Totaal Licht (Te bestellen)
Houten plaat | In bezit | 1 | 2 | 2 | 2 | 0 | € 0,00 | € 0,00 | - € | € 243,21
Main connector | In bezit | Mouser | 0 | 1 | 1 | 1 | € 13,35 | € 13,35 | 13,35 €
Netsnoer | In bezit | 0 | 1 | 2 | 1 | 0 - | - | -
Connectoren kast | In bezit | tinytronics | 1 | 4 | 4 | 4 | € 2,00 | € 8,00 | 8,00 €
conectoren led pcb's | In bezit | tinytronics | 6 | 9 | 9 | 9 | € 0,60 | € 5,40 | 5,40 €
12v 3A supply voor water en planten | In bezit | Mouser | 0 | 1 | 1 | 1 | € 16,52 | € 16,52 | 16,52 €
24v 4.2 A supply voor verlichting | In bezit | Mouser | 0 | 1 | 1 | 1 | € 23,81 | € 23,81 | 23,81 €
Fuse voor main connector | In bezit | Mouser | 1 | 1 | 1 | 1 | € 5,22 | € 5,22 | 5,22 €
Knop | In bezit | Mouser | 1 | 2 | 2 | 2 | € 0,30 | € 0,60 | 0,60 €
Stencils | In bezit | 2 | 2 | € 13,23 | € 13,23 | 26,46 €
Thermische Lijm | In bezit | RS | 1 | 1 | € 10,25 | € 10,25 | € 10,25

Componenten LED-PCB
Led PCB | In bezit | PCBWay | 5 | 10 | 10 | 10 | € 0,44 | € 4,41 | 4,41 € | 15 ipv 10?
Ver rode leds | In bezit | Ver rode leds Mouser | 20 | 40 | 40 | 40 | € 0,28 | € 11,36 | 11,36 €
Rode leds | In bezit | Rode leds Mouser | 30 | 60 | 60 | 60 | € 0,27 | € 15,96 | 15,96 €
Blauwe leds | In bezit | Blauwe leds Mouser | 20 | 40 | 40 | 40 | € 0,21 | € 8,44 | 8,44 €
Heatsink LED-PCB | In bezit | RS | 1 | 1 | 1 | 1 | € 37,94 | € 37,94 | 37,94 €
Thermal Pad LED-PCB | In bezit | RS | 1 | 2 | 2 | 2 | € 21,81 | € 43,62 | 43,62 €
Componenten Driver-PCB
Driver PCB | In bezit | PCBWay | 5 | 10 | 10 | 10 | € 0,44 | € 4,41 | 4,41 €
LDO voor ESP | In bezit | Mouser | 0 | 1 | 1 | 1 | € 0,71 | € 0,71 | 0,71 €
ESP-WROOM-32 | In bezit | 1 | 2 | 2 | 2 | 0 | € 0,00 | € 0,00 | - €
Connector driver pcb | In bezit | tinytronics | 1 | 2 | 2 | 2 | € 0,30 | € 0,60 | 0,60 €
Driver IC | In bezit | Mouser | 5 | 10 | 10 | 10 | € 0,48 | € 4,84 | 4,84 €
LDO voor ESP | In bezit | Mouser | 1 | 2 | 2 | 2 | € 0,66 | € 1,31 | 1,31 €
Driver Heatsink | In bezit | | | | | | | | | Nog aanvullen

Componenten per Driver-PCB
Footprint | Value | References
CAPC2013X95X50LL10T25 | Capacitor 100 nF +/-10% 50 V 0805C1, C2, C3, C4, C5 | 5
AL1793AFE13 | IC1_1, IC1_2, IC1_3 | 3
ESPWROOM32D | IC2 | 1
UA78M33IKVURG3 | Voltage Regulator | IC3 | 1
2828346 | Connector | J1_1, J1_2, J1_3 | 3
282834-2_1 | Connector | J2 | 1
61300411121 | Pin Header | P1 | 1
Resistors | Resistors | R1_1, R1_2, R1_3, R2_1, R2_2, R2_3, R3_1, R3_2, R3_3, R4_1, R4_2, R4_3, R5_1, R5_2, R5_3, R6_1, R6_2, R6_3, R7_1, R7_2, R7_3, R8 | 22
FSM4JSMATR | Micro Miniature Push Button Switch FSM JSM, 50 mA, -35 to 85 degC, 4-Pin SMD, RoHS, Tape and Reel SW1 | 1
Componenten per LED-PCB
Footprint | Value | References
282834-6 | Connector | J0, J1 | 2
JE2835ARY-N-0002A0000-N0000001 | LED | B0, B1, B2 | 3
JE2835AFR-N-0001A0000-N0000001 | LED | FR0, FR1, FR2, FR3 | 4
JE2835AHR-N-0001A0000-N0000001 | LED | R0, R1, R2, R3, R4 | 5
KAST | | | | | | | | | | | Totaal Buitenkast (Te bestellen)
€ 312,59
Hout binnenkast (schatting) | Resthout
| afmetingen | aantal
2000x600x18 | 4
Oude laden | 6

Gextrudeerde aluminium profielen
| afmetingen | aantal
2200x90x45 | 4
640x90x45 | 4
550x90x45 | 4
Wieltjes
Draaiend | 2
Vast | 2

Houtschroeven

DEUR
lengte | aantal
deurkader (sectie 18 mm x 60mm)
2,294 | 2 | 4,588
2,33 | 2 | 4,66
0,732 | 2 | 1,464
2,194 | 1 | 2,194
0,56 | 1 | 0,56
0,736 | 1 | 0,736
Totaal: | lengte | 14,202 m
breedte | 0,06 m
opp | 0,85212 m^2 | € 95,79 eenheidsprijs/m2 eurabo
prijs | € 81,62
aantal
klepscharnieren | 14 | € 4,69 | € 65,66 | Scharnieren

MMLAB plaat 840 x 1200 x 6
| 2 | € 42,12 | € 84,24

ZIJKANTEN: fineerplaten op kaders
breedte | 0,73 m
hoogte | 2,33 m
aantal | 2
opp | 3,4018 m2 | € 23,83 eenheidsprijs CRAS Merelbeke
| prijs | | € 81,06
Blachon | | | | Blanchon

gerecupereerd

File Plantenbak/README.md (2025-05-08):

# Plantenbak 🌱

Onze groep bestaat uit:
- Beau Forrez
- Elias Neels
- Wout Batsele
- Sander De Stercke
- Wouter Fouquet

Meer info vindt u [hier](https://vertical-farming-ib3.github.io/Plantenbak/).

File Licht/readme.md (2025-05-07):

Het team bestaat uit:
- Daan Vercammen
- Andres Bosman
- Syme Vandenbosch
- Arne Van der Stede
- Cas Truyers
- Stijn Verhaeghe

Meer info [hier](https://vertical-farming-ib3.github.io/Licht/).

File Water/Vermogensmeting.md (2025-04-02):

### Stroommeting - Berekende Resultaten

We meten het vermogen door de stroom te meten en deze te vermenigvuldigen met de spanning. De stroom wordt gemeten door een ACS712 sensor. Deze meet aan de hand van het Hall-effect een stroom tot 5 A. Wij zullen echter nooit een stroom van 3 A overtreffen (in uiterste gevallen). Om de analoge uitgangsspanning van deze sensor te beperken tot het bereik van de ADC van de ESP maken we gebruik van een spanningsdeler. Deze bestaat uit een 100k en een 10k weerstand.

We legden verschillende lasten aan om tot onderstaande gegevens te komen.

| Stroom (A) | Gemeten Spanning (V) | Voorspelde Stroom (A) | Afwijking (%) | Vermogen (W) | Opmerkingen |
|---|---|---|---|---|---|
| 0.032 | 2.34 | 0.047 | -46.88 | 0.56 | Grote afwijking bij lage stroom |
| 0.252 | 2.37 | 0.231 | 8.33 | 2.77 | |
| 0.56 | 2.43 | 0.598 | -6.79 | 7.18 | |
| 0.96 | 2.50 | 1.026 | -6.88 | 12.31 | |
| 1.06 | 2.51 | 1.088 | -2.64 | 13.06 | |
| 1.28 | 2.54 | 1.271 | 0.70 | 15.25 | Meest nauwkeurig |
| 1.66 | 2.60 | 1.638 | 1.33 | 19.66 | |
| 1.86 | 2.63 | 1.821 | 2.10 | 21.85 | |
| 2.06 | 2.67 | 2.066 | -0.29 | 24.79 | |

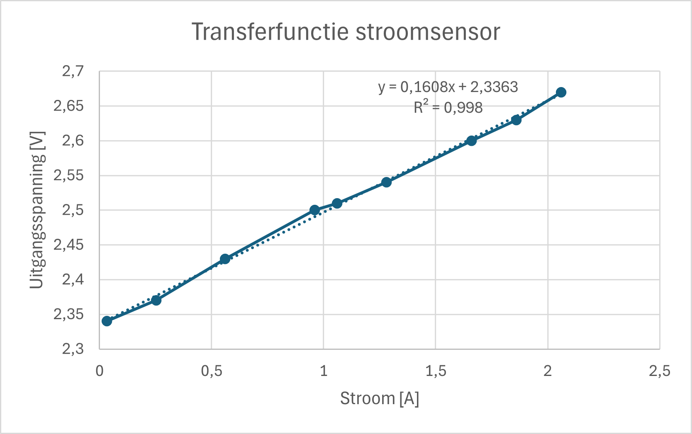
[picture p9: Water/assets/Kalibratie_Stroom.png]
Stroommeting Grafiek
  

**Berekeningsmethoden:**
- **Voorspelde Stroom (A):**  
  `(Gemeten Spanning - 2.3323) / 0.1634`  

- **Afwijking (%):**  
  `(1 - (Voorspelde Stroom / Gemeten Stroom)) × 100`  

- **Vermogen (W):**  
  `Voorspelde Stroom × 12V`  
  Ideaal meten we ook analoog de ingangsspanning op (met een spanningsdeler). We veronderstellen nu echter een constante ingangsspanningvan 12V.

**Conclusies:**
1. Het model is het meest nauwkeurig bij hogere stromgen.
2. Grote afwijkingen treden op bij lage stromen (-46.88% bij 0.032A)
3. Vermogensberekening is consistent gebaseerd op de voorspelde stroom

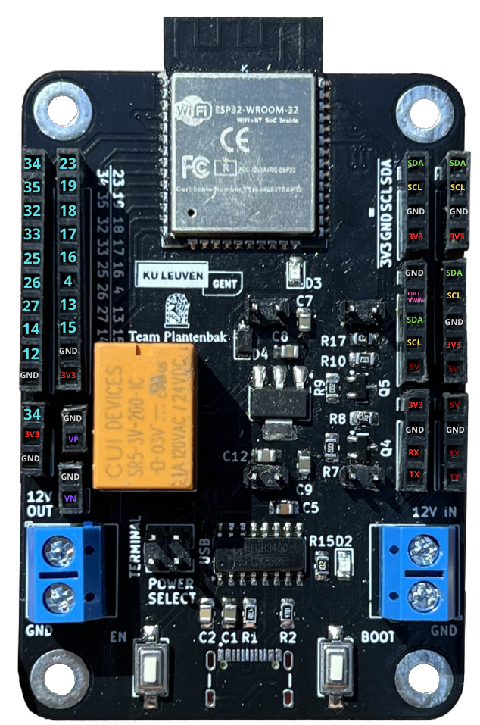
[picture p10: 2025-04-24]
Plantenbak/PCB/pinout.png

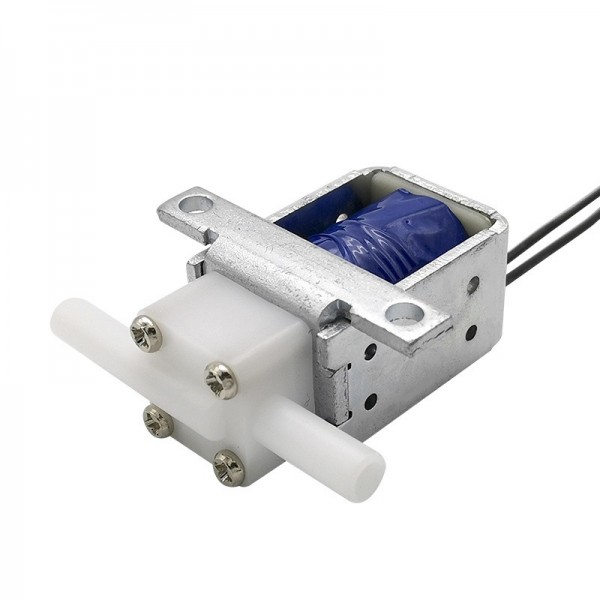
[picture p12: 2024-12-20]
Water/assets/Magneetventiel.jpg

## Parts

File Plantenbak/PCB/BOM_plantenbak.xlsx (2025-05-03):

Footprint | Value | References
Capacitor_SMD:C_0805_2012Metric_Pad1.18x1.45mm_HandSolder | 10u | C1 C7 C8 C9 C12
Capacitor_SMD:C_0805_2012Metric_Pad1.18x1.45mm_HandSolder | 100n | C2 C3 C10 C11
Capacitor_SMD:C_0805_2012Metric_Pad1.18x1.45mm_HandSolder | 1u | C5
Capacitor_SMD:C_0805_2012Metric_Pad1.18x1.45mm_HandSolder | 100u | C6
Diode_SMD:D_SOD-323_HandSoldering | D_Schottky | D1 D4
LED_SMD:LED_0805_2012Metric_Pad1.15x1.40mm_HandSolder | LED | D2 D3
Diode_SMD:D_SOD-123 | 1N4148W | D5
Connector_PinHeader_2.54mm:PinHeader_1x02_P2.54mm_Vertical | Conn_01x02 | J2 J3
Connector_PinHeader_2.54mm:PinHeader_1x04_P2.54mm_Vertical | Conn_01x04 | J4 J8 J14 J15
Connector_PinHeader_2.54mm:PinHeader_1x05_P2.54mm_Vertical | Conn_01x05 | J5 J7
Connector_PinHeader_2.54mm:PinHeader_1x10_P2.54mm_Vertical | Conn_01x10 | J6 J10
TerminalBlock_Phoenix:TerminalBlock_Phoenix_MKDS-1 | Screw_Terminal_01x02 | J9 J11
Connector_PinHeader_2.54mm:PinHeader_2x02_P2.54mm_Vertical | Conn_02x02_Counter_Clockwise | J12
Connector_PinHeader_2.54mm:PinHeader_1x03_P2.54mm_Vertical | Conn_01x03 | J13
Package_TO_SOT_SMD:SOT-23 | BSS138 | Q1 Q2 Q3 Q4 Q5
Resistor_SMD:R_0805_2012Metric_Pad1.20x1.40mm_HandSolder | 4K7 | R1 R2 R5 R6
Resistor_SMD:R_0805_2012Metric_Pad1.20x1.40mm_HandSolder | 1M | R3
Resistor_SMD:R_0805_2012Metric_Pad1.20x1.40mm_HandSolder | 10K | R4 R7 R8 R9 R10 R11 R12 R14 R16
Resistor_SMD:R_0805_2012Metric_Pad1.20x1.40mm_HandSolder | 1K | R13 R15 R17
434111043826:434111043826 | SW_Push | SW1 SW2
Watersysteem_Footprints_Library:MP1584_Module | MP1584_Module | U1
Package_TO_SOT_SMD:SOT-223-3_TabPin2 | AMS1117-3.3 | U2
RF_Module:ESP32-WROOM-32E | ESP32-WROOM-32E | U4

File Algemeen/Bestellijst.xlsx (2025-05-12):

Component | Status | Link | Aantal/module plantenbak | Aantal/module kast | Aantal in bezit | Totaal aantal | Totaal aantal te bestellen | Prijs/eenheid | Kost | Prijs | Info | Totaal Watersysteem (Te bestellen) | Aantal modules kast:
WATERSYSTEEM |  |  |  |  |  |  |  |  |  |  |  | €123.39 | 1
Waterpomp (12VDC) | In bezit | TinyTronics (https://www.tinytronics.nl/nl/mechanica-en-actuatoren/motoren/pompen/waterpomp-12v) |  | 4 |  | 4 | 4 | €6.00 | €24.00 | €24.00 |  |  | Aantal modules plantenbak per module kast:
Aquariumpomp (mengen) | In bezit | TinyTronics (https://www.tinytronics.nl/nl/mechanica-en-actuatoren/motoren/pompen/onderwaterpomp-horizontaal-3-6v) |  | 1 |  | 1 | 1 | €4.00 | €4.00 | €4.00 |  |  | 2
Sensor ISE-2922 NO3- | In bezit | MTLAB (http://www.measureteq.com/electrode-and-sensor/ion-selective-electrode/ise-2922-no3-nitrate-ion-selective-electrode.html) |  | 1 | 1 | 1 | 0 | €36.83 | €36.83 | €0.00 |  |  | Totaal aantal modules plantenbak:
Sensor ISE-2923 Ca2+ | In bezit | MTLAB (http://www.measureteq.com/electrode-and-sensor/ion-selective-electrode/ise-2923-calcium-ion-selective-electrode-ise.html) |  | 1 | 1 | 1 | 0 | €27.62 | €27.62 | €0.00 |  |  | 2
Sensor ISE-2920 K+ | In bezit | MTLAB (http://www.measureteq.com/electrode-and-sensor/ion-selective-electrode/ise-2920-potassium-ion-selective-electrode.html) |  | 1 | 1 | 1 | 0 | €32.22 | €32.22 | €0.00
ADC | In bezit |  |  | 1 | 1 | 1 | 0 | €0.00 | €0.00 | €0.00 | op pcb
UV | Kapot | Aliexpress (https://nl.aliexpress.com/item/1005004493335123.html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) |  | 1 |  | 1 | 1 | €10.43 | €10.43 | €10.43 |  |  | TOTAAL TE BESTELLEN: | Excl verzending, excl xtra kosten, incl btw
Waterhoogte sensor: Ultrasoon | In bezit | TinyTronics (https://www.tinytronics.nl/nl/sensoren/afstand/ultrasonische-afstandssensor-rcwl-1604) |  | 3 | 3 | 3 | 0 | €2.75 | €8.25 | €0.00 |  |  | €766.62
QuickConnect | In bezit | Aliexpress (https://nl.aliexpress.com/item/1005005808872752.html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) | 2 | 4 |  | 4 | 1 | €0.97 | €3.88 | €0.97 | PU-8 voor 8 mm OD (1x 10 stuks bestellen)
Waterslang (6mm ID-8mm OD) | In bezit | TinyTronics (https://www.tinytronics.nl/nl/mechanica-en-actuatoren/onderdelen/slangen/waterslang-voor-onderwaterpomp-verticaal-horizontaal-3-6v-transparant-1-meter) |  | 6 |  | 6 | 6 | €1.50 | €9.00 | €9.00 | per meter (AAN 1 STUK BESTELLEN!)
Silicone kit | In bezit | Hubo (https://www.hubo.be/nl/p/hubo-siliconenkit-sanitair-310ml-transparant/12507/) |  | 1 | 1 | 1 | 0 | €6.50 | €6.50 | €0.00
Klemringen/Slangklemmen | In bezit | Aliexpress (https://nl.aliexpress.com/item/1005007403359089.html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) |  | 1 |  | 1 | 1 | €2.33 | €2.33 | €2.33 | Per 10
Reservoir | In bezit | Vorig jaar |  | 4 | 4 | 4 | 0 | €2.99 | €11.96 | €0.00
Luchtsteen | In bezit | Aliexpress (https://nl.aliexpress.com/item/1005007443597285.html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) |  | 2 |  | 2 | 2 | €0.97 | €1.94 | €1.94
T-stuk (luchtsteen) | In bezit | Aliexpress (https://nl.aliexpress.com/item/32900110036.html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) |  | 1 |  | 1 | 1 | €0.97 | €0.97 | €0.97
Luchtpomp | In bezit | TinyTronics (https://www.tinytronics.nl/nl/mechanica-en-actuatoren/motoren/pompen/luchtpomp-pyp370-12z-12v) |  | 2 |  | 2 | 2 | €4.50 | €9.00 | €9.00
Waterslang (3.5mm ID-Xmm OD) | In bezit | TinyTronics (https://www.tinytronics.nl/nl/mechanica-en-actuatoren/onderdelen/slangen/lucht-water-slang-3.5mm-transparant-1m) |  | 1 |  | 1 | 1 | €2.00 | €2.00 | €2.00 | per meter, 3.5mm
Eindloopschakelaar | In bezit | Hobbyelectronica (https://www.hobbyelectronica.nl/product/3d-printer-endstop-mechanisch-ramps-1-4/) |  | 3 | 3 | 3 | 0 | €1.95 | €5.85 | €0.00
PCB | In bezit | PCBWay (https://www.pcbway.com/) |  | 1 |  | 1 | 1 | €4.39 | €4.39 | €4.39
Relais 5V | In bezit | Mouser (https://www.mouser.be/ProductDetail/Amphenol-Anytek/AHQSS105DM2FA0G) |  | 10 |  | 10 | 10 | €1.47 | €14.70 | €14.70
Waterslang | In bezit | tinytronics (https://www.tinytronics.nl/nl/mechanica-en-actuatoren/onderdelen/slangen/waterslang-voor-onderwaterpomp-verticaal-horizontaal-3-6v-transparant-1-meter) |  | 1 |  | 1 | 1 | €1.50 | €1.50 | €1.50
PPF | In bezit | AliExpress (https://nl.aliexpress.com/item/1005008183056175.html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) |  | 5 |  | 5 | 5 | €0.75 | €3.80 | €3.80
PH- sensor + ADC | In bezit | AliExpress (https://nl.aliexpress.com/item/1005006063176996.html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) |  | 1 |  |  | 1 | €4.52 | €4.52 | €4.52
UV-C filter (nieuw) [14W - ordinary] | In bezit | AliExpress (https://nl.aliexpress.com/item/1005006110975582.html?scm_id=1007.40050.354490.0&scm-url=1007.40050.354490.0) |  | 1 |  |  | 1 | €29.84 | €29.84 | €29.84
Componenten PCB
Footprint | Value | References |  |  |  |  |  |  |  |  | Aanwezig op campus
C_0805_2012Metric_Pad1.18x1.45mm_HandSolder | 100n | C3, C4, C6, C7, C10, C11, C12, C13, C14 |  | 9 | 9 | 9 | 0 | - | - | -
CP_Elec_6.3x3.9 | 100u | C1, C2 |  | 2 | 2 | 2 | 0 | - | - | -
C_0805_2012Metric_Pad1.18x1.45mm_HandSolder | 10u | C5, C9 |  | 2 | 2 | 2 | 0 | - | - | -
CP_EIA-3528-12_Kemet-T_Pad1.50x2.35mm_HandSolder | 22u | C8 |  | 1 | yyyyy | 1 | 0 | - | - | -
R_0805_2012Metric_Pad1.20x1.40mm_HandSolder | 10k | R2, R4, R5, R6, R7, R8, R9, R11, R13 |  | 9 | 9 | 9 | 0 | - | - | -
R_0805_2012Metric_Pad1.20x1.40mm_HandSolder | 470 | R1, R3, R14, R15 |  | 4 | 4 | 4 | 0 | - | - | -
R_0805_2012Metric_Pad1.20x1.40mm_HandSolder | 4.7k | R10, R12 |  | 2 | 2 | 2 | 0 | - | - | -
D_0805_2012Metric_Pad1.15x1.40mm_HandSolder | 1N4148 | D4, D5, D6, D7, D8, D9, D10 |  | 7 | 7 | 7 | 0 | - | - | -
LED_0805_2012Metric_Pad1.15x1.40mm_HandSolder | PWR | D1 |  | 1 | 1 | 1 | 0 | - | - | -
LED_0805_2012Metric_Pad1.15x1.40mm_HandSolder | LED | D2 |  | 1 | 1 | 1 | 0 | - | - | -
DIOM5226X290N | SK36A | D3 |  | 1 | 1 | 1 | 0 | - | - | -
MP1584_Module | MP1584_Module | U1 |  | 1 | 1 | 1 | 0 | - | - | -
ESP32-WROOM-32D | ESP32-WROOM-32D | U2 |  | 1 | 1 | 1 | 0 | - | - | -
TSSOP-10_3x3mm_P0.5mm | ADS1115IDGS | U3 |  | 1 | 1 | 1 | 0 | - | - | -
SOT-223-3_TabPin2 | AMS1117-3.3 | U4 |  | 1 | 1 | 1 | 0 | - | - | -
SOIC-28W_7.5x17.9mm_P1.27mm | MCP23017_SO | U5 |  | 1 | 1 | 1 | 0 | - | - | -
Wurth_Tactile_Switch_SPST-NO_434111043826 | EN | SW1 |  | 1 | 1 | 1 | 0 | - | - | -
Wurth_Tactile_Switch_SPST-NO_434111043826 | BOOT | SW2 |  | 1 | 1 | 1 | 0 | - | - | -
AHQSS105DM2FA0G | AHQSS105DM2FA0G | K1, K2, K3, K4, K5, K6, K7 |  | 7 | 7 | 7 | 0 | - | - | -
SOT-23 | BSS138 | Q1, Q2, Q3, Q4, Q5, Q6, Q7 |  | 7 | 7 | 7 | 0 | - | - | -
MountingHole_3.2mm_M3_Pad_TopBottom | MountingHole_Pad | H1, H2, H3, H4 |  | 4 | 4 | 4 | 0 | - | - | -
SolderJumper-2_P1.3mm_Open_RoundedPad1.0x1.5mm | SolderJumper_2_Open | JP1, JP2, JP3, JP4 |  | 4 | 4 | 4 | 0 | - | - | -
TestPoint_Pad_D2.0mm | TestPoint | TP1, TP2, TP3, TP4 |  | 4 | 4 | 4 | 0 | - | - | -
PinHeader_1x04_P2.54mm_Vertical | Height Water | J1 |  | 1 | 1 | 1 | 0 | - | - | -
PinHeader_1x04_P2.54mm_Vertical | Height Nutrients | J2 |  | 1 | 1 | 1 | 0 | - | - | -
PinHeader_1x04_P2.54mm_Vertical | Height Mixer | J3 |  | 1 | 1 | 1 | 0 | - | - | -
PinHeader_1x02_P2.54mm_Vertical | TestPins | J4 |  | 1 | 1 | 1 | 0 | - | - | -
TerminalBlock_Phoenix_PT-1,5-2-5.0-H_1x02_P5.00mm_Horizontal | 12V ingang | J5 |  | 1 | 1 | 1 | 0 | - | - | -
TerminalBlock_Phoenix_PT-1,5-2-5.0-H_1x02_P5.00mm_Horizontal | Pomp1 | J6 |  | 1 | 1 | 1 | 0 | - | - | -
PinHeader_1x04_P2.54mm_Vertical | TTL Connector | J7 |  | 1 | 1 | 1 | 0 | - | - | -
PinHeader_1x03_P2.54mm_Vertical | Endstop UV | J8 |  | 1 | 1 | 1 | 0 | - | - | -
PinHeader_1x03_P2.54mm_Vertical | Endstop Lade1 | J9 |  | 1 | 1 | 1 | 0 | - | - | -
BNC_Amphenol_B6252HB-NPP3G-50_Horizontal | ReferentieProbe | J10 |  | 1 | 1 | 1 | 0 | - | - | -
PinHeader_1x03_P2.54mm_Vertical | Endstop Lade0 | J11 |  | 1 | 1 | 1 | 0 | - | - | -
TerminalBlock_Phoenix_PT-1,5-2-5.0-H_1x02_P5.00mm_Horizontal | Pomp2 | J12 |  | 1 | 1 | 1 | 0 | - | - | -
PinHeader_1x02_P2.54mm_Vertical | LED Water Level | J13 |  | 1 | 1 | 1 | 0 | - | - | -
PinHeader_1x02_P2.54mm_Vertical | LED Nutrient Level | J14 |  | 1 | 1 | 1 | 0 | - | - | -
BNC_Amphenol_B6252HB-NPP3G-50_Horizontal | Voedingsstoffen 1 | J15 |  | 1 | 1 | 1 | 0 | - | - | -
TerminalBlock_Phoenix_PT-1,5-2-5.0-H_1x02_P5.00mm_Horizontal | Pomp3 | J16 |  | 1 | 1 | 1 | 0 | - | - | -
TerminalBlock_Phoenix_PT-1,5-2-5.0-H_1x02_P5.00mm_Horizontal | Pomp4 | J17 |  | 1 | 1 | 1 | 0 | - | - | -
PinHeader_1x06_P2.54mm_Vertical | Backup GPIO | J18 |  | 1 | 1 | 1 | 0 | - | - | -
BNC_Amphenol_B6252HB-NPP3G-50_Horizontal | Voedingsstoffen 2 | J19 |  | 1 | 1 | 1 | 0 | - | - | -
TerminalBlock_Phoenix_PT-1,5-2-5.0-H_1x02_P5.00mm_Horizontal | Luchtpomp | J20 |  | 1 | 1 | 1 | 0 | - | - | -
BNC_Amphenol_B6252HB-NPP3G-50_Horizontal | Voedingsstoffen 3 | J21 |  | 1 | 1 | 1 | 0 | - | - | -
TerminalBlock_Phoenix_PT-1,5-2-5.0-H_1x02_P5.00mm_Horizontal | Mixer | J22 |  | 1 | 1 | 1 | 0 | - | - | -
TerminalBlock_Phoenix_PT-1,5-2-5.0-H_1x02_P5.00mm_Horizontal | 230V | J23 |  | 1 | 1 | 1 | 0 | - | - | -
TerminalBlock_Phoenix_PT-1,5-2-5.0-H_1x02_P5.00mm_Horizontal | UV | J24 |  | 1 | 1 | 1 | 0 | - | - | -
PLANTENBAK |  |  |  |  |  |  |  |  |  |  |  | Totaal Plantenbak (Te bestellen)
Capacitive soil moisture sensor | In bezit |  | 1 | 2 | 2 | 2 |  |  |  |  |  | €87.43
GY-SCD40 module | In bezit |  | 1 | 2 | 2 | 2
NFC-reader PN532 | In bezit |  | 1 | 2 | 2 | 2
NFC-tags | In bezit |  | 1 | 2 | 2 | 2
Nieuwe PCB's | In bezit | PCBWay (https://www.pcbway.com/) | 1 | 2 |  | 2 | 2 |  |  | €4.39
BH1750 lichtsensor | In bezit | Hobbyelectronica (https://www.hobbyelectronica.nl/product/bh1750-digitale-licht-sensor/) | 1 | 2 |  | 2 | 2 | €2.25 | €4.50 | €4.50
CH340C | In bezit | AliExpress (https://www.aliexpress.com/item/1005006040438712.html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) | 1 | 2 |  | 10 | 10 | €0.41 | €4.05 | €4.05
ESP-WROOM-32 | In bezit
Ventilatoren (12V) | In bezit |  | 2 | 4 |  | 4 | 4
Relais SR5 | In bezit | Digikey (https://www.digikey.be/en/products/detail/same-sky-formerly-cui-devices/SR5-3V-200-1C/16602081) | 1 | 2 |  | 2 | 2 | €1.13 | €2.26 | €2.26
MP1584 | In bezit | TinyTronics (https://www.tinytronics.nl/en/power/voltage-converters/buck-(step-down)-converters/mini-dc-dc-adjustable-step-down-buck-converter-1a-mp1584) | 1 | 2 |  | 2 | 2 | €1.50 | €3.00 | €3.00
Dupont kabels | In bezit |  |  |  |  | 4 | 4 | €2.00 | €8.00 | €8.00
5V relais | In bezit | Tinytronics (https://www.tinytronics.nl/nl/schakelaars/relais/relais-modules/5v-relais-1-channel-hoog-actief-of-laag-actief) |  |  |  | 2 | 2 | €2.50 | €5.00 | €5.00
Rockwool aliexpress | In bezit | AliExpress (https://www.aliexpress.com/item/1005007321849079.html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) |  |  |  | 1 | 1 | €4.65 | €4.65 | €4.65 | 100 stuks per batch
Potjes voor plantjes: NO.40 white | In bezit | AliExpress (https://nl.aliexpress.com/item/1005004666016798.html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) |  |  |  | 2 | 2 | €3.28 | €3.28 | €6.56 | NO.50 white (15 stuk per batch)
Witte verf | In bezit | Action (https://www.action.com/nl-be/p/3015431/spectrum-2-in-1-hoogglans-verf-wit/) |  |  |  | 1 | 1 | €7.99 | €7.99 | €7.99
Verfborstel en verfbak | In bezit | action |  |  |  | 1 | 1 | €1.84 | €1.84 | €1.84
Kokosvezel potgrond | In bezit | Action (https://www.action.com/nl-be/p/2520586/kokos-potgrond/) |  |  |  | 3 | 3 | €1.17 | €3.51 | €3.51
Plantenvoeding | In bezit | Action (https://www.action.com/nl-be/p/3004917/green-boots-biologische-plantenvoeding-voor-groenten/) |  |  |  | 2 | 2 | €1.79 | €3.58 | €3.58
Bloempotjes | In bezit | action |  |  |  | 2 | 2 | €1.11 | €2.22 | €2.22
Hydrokorrels | In bezit | Action (https://www.action.com/nl-be/p/2562268/hydrokorrels/) |  |  |  | 1 | 1 | €2.37 | €2.37 | €2.37
Glasbokalen | In bezit | Action (https://www.action.com/nl-be/p/2552569/voorraadpot/) |  |  |  | 9 | 9 | €0.89 | €8.01 | €8.01
Kitlijm voor bakken | In bezit | Gamma |  |  |  | 1 | 1 | €11.00 | €11.00 | €11.00
Regentonkraan voor bakken | In bezit | EuroShop |  |  |  | 1 | 1 | €4.50 | €4.50 | €4.50
Componenten PCB
Footprint | Value | References |  |  |  |  |  |  |  |  | Aanwezig op campus
Capacitor_SMD:C_0805_2012Metric_Pad1.18x1.45mm_HandSolder | 10u | C1 C7 C8 C9 C12 | 5 | 10 | 10 | 10 | 0
Capacitor_SMD:C_0805_2012Metric_Pad1.18x1.45mm_HandSolder | 100n | C2 C3 C10 C11 | 4 | 8 | 8 | 8 | 0
Capacitor_SMD:C_0805_2012Metric_Pad1.18x1.45mm_HandSolder | 1u | C5 | 1 | 2 | 2 | 2 | 0
Capacitor_SMD:C_0805_2012Metric_Pad1.18x1.45mm_HandSolder | 100u | C6 | 1 | 2 | 2 | 2 | 0
Diode_SMD:D_SOD-323_HandSoldering | D_Schottky | D1 D4 | 2 | 4 | 4 | 4 | 0
LED_SMD:LED_0805_2012Metric_Pad1.15x1.40mm_HandSolder | LED | D2 D3 | 2 | 4 | 4 | 4 | 0
Diode_SMD:D_SOD-123 | 1N4148W | D5 | 1 | 2 | 2 | 2 | 0
Connector_PinHeader_2.54mm:PinHeader_1x02_P2.54mm_Vertical | Conn_01x02 | J2 J3 | 2 | 4 | 4 | 4 | 0
Connector_PinHeader_2.54mm:PinHeader_1x04_P2.54mm_Vertical | Conn_01x04 | J4 J8 J14 J15 | 4 | 8 | 8 | 8 | 0
Connector_PinHeader_2.54mm:PinHeader_1x05_P2.54mm_Vertical | Conn_01x05 | J5 J7 | 2 | 4 | 4 | 4 | 0
Connector_PinHeader_2.54mm:PinHeader_1x10_P2.54mm_Vertical | Conn_01x10 | J6 J10 | 2 | 4 | 4 | 4 | 0
TerminalBlock_Phoenix:TerminalBlock_Phoenix_MKDS-1 | Screw_Terminal_01x02 | J9 J11 | 2 | 4 | 4 | 4 | 0
Connector_PinHeader_2.54mm:PinHeader_2x02_P2.54mm_Vertical | Conn_02x02_Counter_Clockwise | J12 | 1 | 2 | 2 | 2 | 0
Connector_PinHeader_2.54mm:PinHeader_1x03_P2.54mm_Vertical | Conn_01x03 | J13 | 1 | 2 | 2 | 2 | 0
Package_TO_SOT_SMD:SOT-23 | BSS138 | Q1 Q2 Q3 Q4 Q5 | 5 | 10 | 10 | 10 | 0
Resistor_SMD:R_0805_2012Metric_Pad1.20x1.40mm_HandSolder | 4K7 | R1 R2 R5 R6 | 4 | 8 | 8 | 8 | 0
Resistor_SMD:R_0805_2012Metric_Pad1.20x1.40mm_HandSolder | 1M | R3 | 1 | 2 | 2 | 2 | 0
Resistor_SMD:R_0805_2012Metric_Pad1.20x1.40mm_HandSolder | 10K | R4 R7 R8 R9 R10 R11 R12 R14 R16 | 9 | 18 | 18 | 18 | 0
Resistor_SMD:R_0805_2012Metric_Pad1.20x1.40mm_HandSolder | 1K | R13 R15 R17 | 3 | 6 | 6 | 6 | 0
434111043826:434111043826 | SW_Push | SW1 SW2 | 2 | 4 | 4 | 4 | 0
Watersysteem_Footprints_Library:MP1584_Module | MP1584_Module | U1 | 1 | 2 | 2 | 2 | 0
Package_TO_SOT_SMD:SOT-223-3_TabPin2 | AMS1117-3.3 | U2 | 1 | 2 | 2 | 2 | 0
RF_Module:ESP32-WROOM-32E | ESP32-WROOM-32E | U4 | 1 | 2 | 2 | 2 | 0
Verlichting en power | nt |  |  |  |  |  |  |  |  |  |  | Totaal Licht (Te bestellen)
Houten plaat | In bezit |  | 1 | 2 | 2 | 2 | 0 | €0.00 | €0.00 | €0.00 |  | €243.21
Main connector | In bezit | Mouser (https://www.mouser.be/ProductDetail/Schurter/KM00.1105.11?qs=h0lr9otJFD6kzO1nFMottA%3D%3D) | 0 | 1 |  | 1 | 1 | €13.35 | €13.35 | €13.35
Netsnoer | In bezit |  | 0 | 1 | 2 | 1 | 0 | - | - | -
Connectoren kast | In bezit | tinytronics (https://www.tinytronics.nl/nl/kabels-en-connectoren/connectoren/gx/gx12/gx12-4-connector-set) | 1 | 4 |  | 4 | 4 | €2.00 | €8.00 | €8.00
conectoren led pcb's | In bezit | tinytronics (https://www.tinytronics.nl/nl/kabels-en-connectoren/connectoren/schroefterminals/6-pin-schroef-terminal-block-connector-2.54mm-afstand) | 6 | 9 |  | 9 | 9 | €0.60 | €5.40 | €5.40
12V 3A supply voor water en planten | In bezit | Mouser (https://www.mouser.be/ProductDetail/TRACO-Power/TXN-35-112) | 0 | 1 |  | 1 | 1 | €16.52 | €16.52 | €16.52
24V 4.2 A supply voor verlichting | In bezit | Mouser (https://www.mouser.be/ProductDetail/TRACO-Power/TXN-100-124) | 0 | 1 |  | 1 | 1 | €23.81 | €23.81 | €23.81
Fuse voor main connector | In bezit | Mouser (https://www.mouser.be/ProductDetail/Schurter/43011403?qs=fxxZwZgTYwA8B4fs8Del4g%3D%3D&gad_source=5) | 1 | 1 |  | 1 | 1 | €5.22 | €5.22 | €5.22
Knop | In bezit | Mouser (https://eu.mouser.com/ProductDetail/TE-Connectivity-Alcoswitch/FSM4JSMATR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) | 1 | 2 |  | 2 | 2 | €0.30 | €0.60 | €0.60
Stencils | In bezit |  |  |  |  | 2 | 2 | €13.23 | €13.23 | €26.46
Thermische Lijm | In bezit | RS (https://benl.rs-online.com/web/p/adhesive-activators-primers-debonders/2384465?gb=s) |  |  |  | 1 | 1 | €10.25 | €10.25 | €10.25
Componenten LED-PCB
Led PCB | In bezit | PCBWay | 5 | 10 |  | 10 | 10 | €0.44 | €4.41 | €4.41 | 15 ipv 10?
Ver rode leds | In bezit | Ver rode leds Mouser (https://www.mouser.be/ProductDetail/Cree-LED/JE2835AFR-N-0001A0000-N0000001?qs=tlsG%2FOw5FFhxeS5Ond46kw%3D%3D) | 20 | 40 |  | 40 | 40 | €0.28 | €11.36 | €11.36
Rode leds | In bezit | Rode leds Mouser (https://www.mouser.be/ProductDetail/Cree-LED/JE2835AHR-N-0001A0000-N0000001?qs=tlsG%2FOw5FFjj3bMznpJhRA%3D%3D) | 30 | 60 |  | 60 | 60 | €0.27 | €15.96 | €15.96
Blauwe leds | In bezit | Blauwe leds Mouser (https://www.mouser.be/ProductDetail/Cree-LED/JE2835ARY-N-0002A0000-N0000001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) | 20 | 40 |  | 40 | 40 | €0.21 | €8.44 | €8.44
Heatsink led-PCB | In bezit | RS (https://benl.rs-online.com/web/p/heatsinks/9033096?gb=s) | 1 | 1 |  | 1 | 1 | €37.94 | €37.94 | €37.94
Thermal Pad led-PCB | In bezit | RS (https://benl.rs-online.com/web/p/thermal-pads/1745714?gb=s) | 1 | 2 |  | 2 | 2 | €21.81 | €43.62 | €43.62
Componenten Driver-PCB
Driver PCB | In bezit | PCBWay | 5 | 10 |  | 10 | 10 | €0.44 | €4.41 | €4.41
LDO voor ESP | In bezit | Mouser (https://www.mouser.be/ProductDetail/onsemi/NCP718BSN330T1G?qs=MLItCLRbWsy3SIiB9fjYCg%3D%3D) | 0 | 1 |  | 1 | 1 | €0.71 | €0.71 | €0.71
ESP-WROOM-32 | In bezit |  | 1 | 2 | 2 | 2 | 0 | €0.00 | €0.00 | €0.00
Connector driver pcb | In bezit | tinytronics (https://www.tinytronics.nl/nl/kabels-en-connectoren/connectoren/schroefterminals/2-pin-schroef-terminal-block-connector-2.54mm-afstand) | 1 | 2 |  | 2 | 2 | €0.30 | €0.60 | €0.60
Driver IC | In bezit | Mouser (https://www.mouser.be/ProductDetail/Diodes-Incorporated/AL1793AFE-13?qs=bKenfurwlskeSg5Tj2A9LQ%3D%3D) | 5 | 10 |  | 10 | 10 | €0.48 | €4.84 | €4.84
LDO voor ESP | In bezit | Mouser (https://www.mouser.be/ProductDetail/Texas-Instruments/UA78M33IKVURG3?qs=dP8SwFlKThxMmGpfgS%2FADQ%3D%3D) | 1 | 2 |  | 2 | 2 | €0.66 | €1.31 | €1.31
Driver Heatsink | In bezit |  |  |  |  |  |  |  |  |  | Nog aanvullen
Componenten per Driver-PCB
Footprint | Value | References
CAPC2013X95X50LL10T25 | Capacitor 100 nF +/-10% 50 V 0805 | C1, C2, C3, C4, C5 |  |  |  | 5
AL1793AFE13 |  | IC1_1, IC1_2, IC1_3 |  |  |  | 3
ESPWROOM32D |  | IC2 |  |  |  | 1
UA78M33IKVURG3 | Voltage Regulator | IC3 |  |  |  | 1
2828346 | Connector | J1_1, J1_2, J1_3 |  |  |  | 3
282834-2_1 | Connector | J2 |  |  |  | 1
61300411121 | Pin Header | P1 |  |  |  | 1
Resistors | Resistors | R1_1, R1_2, R1_3, R2_1, R2_2, R2_3, R3_1, R3_2, R3_3, R4_1, R4_2, R4_3, R5_1, R5_2, R5_3, R6_1, R6_2, R6_3, R7_1, R7_2, R7_3, R8 |  |  |  | 22
FSM4JSMATR | Micro Miniature Push Button Switch FSM JSM, 50 mA, -35 to 85 degC, 4-Pin SMD, RoHS, Tape and Reel | SW1 |  |  |  | 1
Componenten per LED-PCB
Footprint | Value | References
282834-6 | Connector | J0, J1 |  |  |  | 2
JE2835ARY-N-0002A0000-N0000001 | LED | B0, B1, B2 |  |  |  | 3
JE2835AFR-N-0001A0000-N0000001 | LED | FR0, FR1, FR2, FR3 |  |  |  | 4
JE2835AHR-N-0001A0000-N0000001 | LED | R0, R1, R2, R3, R4 |  |  |  | 5
KAST |  |  |  |  |  |  |  |  |  |  |  | Totaal Buitenkast (Te bestellen)
 |  |  |  |  |  |  |  |  |  |  |  | €312.59
Hout binnenkast (schatting) | Resthout
 | afmetingen (mm) | aantal
 | 2000x600x18 | 4
Oude laden |  | 6
Gextrudeerde aluminium profielen
 | afmetingen (mm) | aantal
 | 2200x90x45 | 4
 | 640x90x45 | 4
 | 550x90x45 | 4
Wieltjes
 | Draaiend | 2
 | Vast | 2
Houtschroeven
DEUR
 | lengte | aantal
Deurkader (sectie 18mm x 60mm)
 | 2.294 | 2 | 4.588
 | 2.330 | 2 | 4.660
 | 0.732 | 2 | 1.464
 | 2.194 | 1 | 2.194
 | 0.560 | 1 | 0.560
 | 0.736 | 1 | 0.736
 | Totaal: | lengte | 14.202 | m
 |  | breedte | 0.060 | m
 |  | opp | 0.852 | m2 | €95.79 | eenheidsprijs/m2 Eurabo
 |  |  | prijs |  | €81.62
 |  |  | aantal
Klepscharnieren |  |  | 14 | €4.69 | €65.66 |  | Scharnieren (https://www.meubelbeslagonline.nl/klepscharnier-staal-vernikkeld-gepolijst)
MMLAB plaat 840 x 1200 x 6
 |  |  | 2 | €42.12 | €84.24
ZIJKANTEN: fineerplaten op kaders
 |  | breedte | 0.730 | m
 |  | hoogte | 2.330 | m
 |  | aantal | 2.000
 |  | opp | 3.402 | m2 | €23.83 | eenheidsprijs CRAS Merelbeke
 |  |  | prijs |  | €81.06
Blachon |  |  |  |  |  |  | Blanchon (https://baticolage.com/products/blanchon-huile-environnement-5l?variant=39781262229678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)
 |  |  |  |  | -

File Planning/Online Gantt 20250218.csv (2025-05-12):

Outline Level | ID | Name | Start | Finish | Duration | % Complete | Predecessors | Resource Names | Color | Notes
1 | 1 | Team water | 2024-10-08 | 2025-04-29 | 146 day | 37 |  |  | 211 | <p><br></p>
2 | 2 | Aanpak onderzoek | 2024-10-08 | 2025-02-11 | 91 day | 100 | 57SS | Charlotte Bert,Kjell Naessens,Niels Verhoeve,Sander Haustraete | 211 | <p><br></p>
2 | 3 | Onderzoek componenten | 2024-12-10 | 2025-02-18 | 51 day | 100 | 67SF | Charlotte Bert,Kjell Naessens,Niels Verhoeve,Sander Haustraete | 211 | <p>Deze stap grondig uitvoeren om het risico van niet ideale componenten, niet leverbare componenten te verminderen.<br><br></p>
2 | 4 | Reservoir | 2025-02-18 | 2025-04-29 | 51 day | 2 |  |  | 211 | <p><br></p>
3 | 5 | PCB design | 2025-02-18 | 2025-03-10 | 15 day | 10 | 86SF | Sander Haustraete,Kjell Naessens |  | <p><br></p>
3 | 6 | PCB solderen | 2025-03-31 | 2025-04-08 | 7 day | 0 | 86FS+14 days | Sander Haustraete |  | <p>Er wordt rekening gehouden met levertijd en eventuele vertraging. (Offset van 2 weken)</p>
3 | 87 | Programmeren | 2025-03-11 | 2025-04-08 | 21 day | 0 | 5FS | Kjell Naessens |  | <p><br></p>
3 | 7 | Test en reflectie | 2025-04-09 | 2025-04-29 | 15 day | 0 | 6FS | Charlotte Bert,Kjell Naessens,Niels Verhoeve,Sander Haustraete |  | <p><br></p>
2 | 8 | Toevoer | 2025-02-18 | 2025-04-29 | 51 day | 0 |  |  | 211 | <p><br></p>
3 | 88 | Uitwerken Connectie en leidingen | 2025-02-18 | 2025-03-10 | 15 day | 0 | 3FS-1 days | Charlotte Bert,Niels Verhoeve |  | <p><br></p>
3 | 9 | Connectie | 2025-03-11 | 2025-04-08 | 21 day | 0 | 67FS+14 days | Charlotte Bert,Niels Verhoeve |  | <p><br></p>
3 | 10 | Leidingen | 2025-03-14 | 2025-04-11 | 21 day | 0 | 9SS+3 days | Charlotte Bert,Niels Verhoeve |  | <p><br></p>
3 | 64 | Test en reflectie | 2025-04-14 | 2025-04-29 | 12 day | 0 | 10FS | Charlotte Bert,Niels Verhoeve,Sander Haustraete,Kjell Naessens |  | <p><br></p>
2 | 12 | Afvoer | 2025-02-18 | 2025-04-29 | 51 day | 0 |  |  | 211 | <p><br></p>
3 | 90 | Uitwerken Connectie, leidingen en uitwerking bak | 2025-02-18 | 2025-03-11 | 16 day | 0 | 3FS-1 days | Charlotte Bert,Niels Verhoeve |  | <p><br></p>
3 | 63 | Connectie | 2025-03-11 | 2025-04-08 | 21 day | 0 | 67FS+14 days | Charlotte Bert,Niels Verhoeve |  | <p><br></p>
3 | 13 | Leidingen | 2025-03-14 | 2025-04-11 | 21 day | 0 | 63SS+3 days | Charlotte Bert,Niels Verhoeve |  | <p><br></p>
3 | 68 | Afvoer binnen bak uitvoering | 2025-03-14 | 2025-04-11 | 21 day | 0 | 13SS | Charlotte Bert,Niels Verhoeve |  | <p><br></p>
3 | 61 | Detectie systeem | 2025-03-31 | 2025-04-28 | 21 day | 0 | 6SS | Sander Haustraete |  | <p><br></p>
3 | 66 | Test en reflectie | 2025-04-14 | 2025-04-29 | 12 day | 0 | 13FS | Charlotte Bert,Niels Verhoeve |  | <p><br></p>
1 | 16 | Team verlichting | 2024-10-08 | 2025-04-22 | 141 day | 58 |  |  | 61 | <p><br></p>
2 | 71 | component keuze | 2024-10-08 | 2025-02-18 | 96 day | 100 |  | Andres Bosman,Arne Van der Stede,Cas Truyers,Daan Vercammen,Stijn Verhaeghe,Syme Vandenbosch | 61 | <p><br></p>
2 | 91 | lay-out lade | 2025-02-18 | 2025-02-25 | 6 day | 0 | 71FS-1 days | Andres Bosman,Arne Van der Stede,Cas Truyers,Daan Vercammen,Stijn Verhaeghe,Syme Vandenbosch | 61 | <p><br></p>
2 | 92 | PCB ontwerpen LED | 2025-02-25 | 2025-03-10 | 10 day | 0 | 86SF,91FS-1 days | Daan Vercammen,Cas Truyers | 61 | <p><br></p>
2 | 105 | PCB ontwerpen DRIVER | 2025-02-25 | 2025-03-10 | 10 day | 0 | 86SF,91FS-1 days | Arne Van der Stede,Stijn Verhaeghe | 61 | <p><br></p>
2 | 106 | Thermische berekening | 2025-02-18 | 2025-02-28 | 9 day | 30 |  | Syme Vandenbosch | 61 | <p><br></p>
2 | 93 | PCB solderen | 2025-03-31 | 2025-04-07 | 6 day | 0 | 86FS+14 days | Arne Van der Stede,Cas Truyers,Daan Vercammen,Stijn Verhaeghe,Syme Vandenbosch | 61 | <p><br></p>
2 | 104 | Code | 2025-03-11 | 2025-04-08 | 21 day | 0 | 92FS | Andres Bosman | 61 | <p><br></p>
2 | 94 | Testen en reflecteren | 2025-04-08 | 2025-04-22 | 11 day | 0 | 93FS | Andres Bosman,Arne Van der Stede,Cas Truyers,Daan Vercammen,Stijn Verhaeghe,Syme Vandenbosch | 61 | <p><br></p>
1 | 31 | Team plantenbak | 2024-10-08 | 2025-04-18 | 139 day | 72 |  |  | 91 | <p><br></p>
2 | 70 | BOM | 2024-10-08 | 2025-02-18 | 96 day | 100 | 67SF | Beau Forrez,Elias Neels,Wouter Fouquet,Sander De Stercke,Wout Batselé | 91 | <p><br></p>
2 | 73 | Plantenbak volledig schetsen | 2025-02-18 | 2025-02-18 | 1 day | 100 | 70FS-1 days | Beau Forrez,Elias Neels,Wouter Fouquet,Sander De Stercke,Wout Batselé | 91 | <p><br></p>
2 | 74 | PCB-ontwerp | 2025-03-03 | 2025-03-10 | 6 day | 75 | 86SF | Beau Forrez,Elias Neels,Wout Batselé | 91 | <p><br></p>
2 | 78 | PCB solderen | 2025-03-31 | 2025-04-07 | 6 day | 0 | 86FS+14 days | Beau Forrez,Elias Neels,Wouter Fouquet,Sander De Stercke,Wout Batselé | 91 | <p><br></p>
2 | 81 | ESP testen | 2025-04-08 | 2025-04-15 | 6 day | 0 | 78FS | Beau Forrez,Elias Neels,Wout Batselé | 91 | <p><br></p>
2 | 76 | Humidity sensor testen/coderen | 2025-02-18 | 2025-03-04 | 11 day | 40 |  | Wouter Fouquet,Sander De Stercke | 91 | <p>Component al aanwezig?</p>
2 | 77 | Luchtsensor testen/coderen | 2025-02-18 | 2025-03-04 | 11 day | 40 |  | Wouter Fouquet,Sander De Stercke | 91 | <p>Component al aanwezig?</p>
2 | 79 | NFC-reader testen/coderen | 2025-02-18 | 2025-03-11 | 16 day | 60 |  | Wouter Fouquet,Sander De Stercke | 91 | <p>Component al aanwezig?</p>
2 | 80 | Ventilatoren testen/coderen | 2025-02-18 | 2025-03-11 | 16 day | 40 |  | Wouter Fouquet,Sander De Stercke | 91 | <p>Component al aanwezig?</p>
2 | 82 | Alles samenbrengen en reflecteren | 2025-04-11 | 2025-04-18 | 6 day | 0 | 81FS-3 days | Wouter Fouquet,Sander De Stercke,Beau Forrez,Elias Neels,Wout Batselé | 91 | <p>alleen afhankelijk van esp?</p>
1 | 46 | Team power | 2025-02-18 | 2025-04-21 | 45 day | 17 |  |  | 331 | <p><br></p>
2 | 48 | Lijst van noden opstellen | 2025-02-18 | 2025-02-25 | 6 day | 100 |  | Daan Vercammen | 331 | <p><br></p>
2 | 95 | Componenten lijst opstellen | 2025-02-25 | 2025-03-11 | 11 day | 0 | 48FS-1 days,101SF | Andres Bosman,Cas Truyers,Arne Van der Stede,Daan Vercammen,Stijn Verhaeghe,Syme Vandenbosch | 331 | <p><br></p>
2 | 99 | Indeling uitwerken | 2025-02-18 | 2025-02-24 | 5 day | 52 |  | Arne Van der Stede,Andres Bosman,Stijn Verhaeghe | 331 | <p><br></p>
2 | 96 | PCB design | 2025-02-25 | 2025-03-10 | 10 day | 0 | 86SF | Andres Bosman,Arne Van der Stede,Stijn Verhaeghe | 331 | <p><br></p>
2 | 97 | PCB solderen | 2025-03-31 | 2025-04-04 | 5 day | 0 | 86FS+14 days | Arne Van der Stede,Cas Truyers,Daan Vercammen,Stijn Verhaeghe,Syme Vandenbosch | 331 | <p><br></p>
2 | 98 | Testen en reflecteren | 2025-04-07 | 2025-04-21 | 11 day | 0 | 97FS | Andres Bosman,Arne Van der Stede,Cas Truyers,Daan Vercammen,Stijn Verhaeghe,Syme Vandenbosch | 331 | <p><br></p>
1 | 56 | Ontwerp Samenbrengen | 2024-10-08 | 2025-05-12 | 155 day | 73 |  |  | 301 | <p><br></p>
2 | 57 | Overleg architecten | 2024-10-08 | 2024-12-20 | 54 day | 100 |  | Andres Bosman,Beau Forrez,Charlotte Bert,Wout Batselé,Sander Haustraete,Niels Verhoeve,Kjell Naessens,Elias Neels,Daan Vercammen | 301 | <p><br></p>
2 | 59 | Kast indeling | 2024-10-25 | 2025-03-21 | 106 day | 80 | 99FF+19 days,73FF+20 days,91FF+15 days,90FF+5 days |  | 301 | <p><br></p>
2 | 100 | Power in kast integreren | 2025-04-01 | 2025-04-22 | 16 day | 0 |  |  | 301 | <p><br></p>
2 | 85 | Plantenbak en water samenbrengen | 2025-04-15 | 2025-04-18 | 4 day | 0 | 82FS-6 days,13FS+1 day | Beau Forrez,Elias Neels,Charlotte Bert,Kjell Naessens,Niels Verhoeve,Sander Haustraete,Sander De Stercke,Wouter Fouquet,Wout Batselé | 301 | <p><br></p>
2 | 58 | Kast in elkaar zetten | 2025-04-22 | 2025-04-29 | 6 day | 0 | 103SF-4 days |  | 301 | <p><br></p>
2 | 107 | Reflectie na generale | 2025-05-08 | 2025-05-12 | 3 day | 0 | 102SF,103FS+2 days |  | 301 | <p><br></p>
1 | 89 | PowerPoint maken | 2025-04-28 | 2025-05-05 | 6 day | 0 | 103SF |  | 271 | <p><br></p>
1 | 67 | Bestellijst indienen | 2025-02-18 | 2025-02-18 | 0 day | 0 |  |  |  | <p><br></p>
1 | 101 | Bestellijst indienen power | 2025-03-11 | 2025-03-11 | 0 day | 0 |  |  |  | <p><br></p>
1 | 86 | PCB bestellen | 2025-03-11 | 2025-03-11 | 0 day | 0 |  |  |  | <p>We bestellen deze tijdig omdat dit een cruciaal element is en er genoeg tijd nodig is om fouten recht te zetten.&nbsp;</p>
1 | 103 | Generale repetitie | 2025-05-06 | 2025-05-06 | 0 day | 0 |  |  |  | <p><br></p>
1 | 102 | Eindpresentatie | 2025-05-13 | 2025-05-13 | 0 day | 0 |  |  |  | <p><br></p>

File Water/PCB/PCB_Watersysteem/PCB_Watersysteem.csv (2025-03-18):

Id | Designator | Footprint | Quantity | Designation
1 | J11 | PinHeader_1x03_P2.54mm_Vertical | 1 | Endstop Lade0
2 | J5 | TerminalBlock_Phoenix_PT-1,5-2-5.0-H_1x02_P5.00mm_Horizontal | 1 | 12V ingang
3 | JP4,JP2,JP1,JP3 | SolderJumper-2_P1.3mm_Open_RoundedPad1.0x1.5mm | 4 | SolderJumper_2_Open
4 | J9 | PinHeader_1x03_P2.54mm_Vertical | 1 | Endstop Lade1
5 | SW2 | Wurth_Tactile_Switch_SPST-NO_434111043826 | 1 | BOOT
6 | R1,R3,R15,R14 | R_0805_2012Metric_Pad1.20x1.40mm_HandSolder | 4 | 470
7 | R4,R6,R5,R7,R2,R13,R11,R9,R8 | R_0805_2012Metric_Pad1.20x1.40mm_HandSolder | 9 | 10k
8 | J6 | TerminalBlock_Phoenix_PT-1,5-2-5.0-H_1x02_P5.00mm_Horizontal | 1 | Pomp1
9 | K1,K3,K7,K4,K6,K5,K2 | AHQSS105DM2FA0G | 7 | AHQSS105DM2FA0G
10 | C4,C3,C14,C13,C12,C11,C10,C6,C7 | C_0805_2012Metric_Pad1.18x1.45mm_HandSolder | 9 | 100n
11 | J22 | TerminalBlock_Phoenix_PT-1,5-2-5.0-H_1x02_P5.00mm_Horizontal | 1 | Mixer
12 | J18 | PinHeader_1x06_P2.54mm_Vertical | 1 | Backup GPIO
13 | J24 | TerminalBlock_Phoenix_PT-1,5-2-5.0-H_1x02_P5.00mm_Horizontal | 1 | UV
14 | D1 | LED_0805_2012Metric_Pad1.15x1.40mm_HandSolder | 1 | PWR
15 | D2 | LED_0805_2012Metric_Pad1.15x1.40mm_HandSolder | 1 | LED
16 | H2,H1,H4,H3 | MountingHole_3.2mm_M3_Pad_TopBottom | 4 | MountingHole_Pad
17 | U3 | TSSOP-10_3x3mm_P0.5mm | 1 | ADS1115IDGS
18 | J17 | TerminalBlock_Phoenix_PT-1,5-2-5.0-H_1x02_P5.00mm_Horizontal | 1 | Pomp4
19 | SW1 | Wurth_Tactile_Switch_SPST-NO_434111043826 | 1 | EN
20 | J14 | PinHeader_1x02_P2.54mm_Vertical | 1 | LED Nutrient Level
21 | U1 | MP1584_Module | 1 | MP1584_Module
22 | TP1,TP3,TP4,TP2 | TestPoint_Pad_D2.0mm | 4 | TestPoint
23 | J21 | BNC_Amphenol_B6252HB-NPP3G-50_Horizontal | 1 | Voedingsstoffen 3
24 | J1 | PinHeader_1x04_P2.54mm_Vertical | 1 | Height Water
25 | J23 | TerminalBlock_Phoenix_PT-1,5-2-5.0-H_1x02_P5.00mm_Horizontal | 1 | 230V
26 | C2,C1 | CP_Elec_6.3x3.9 | 2 | 100u
27 | U2 | ESP32-WROOM-32D | 1 | ESP32-WROOM-32D
28 | J8 | PinHeader_1x03_P2.54mm_Vertical | 1 | Endstop UV
29 | J4 | PinHeader_1x02_P2.54mm_Vertical | 1 | TestPins
30 | J10 | BNC_Amphenol_B6252HB-NPP3G-50_Horizontal | 1 | ReferentieProbe
31 | J7 | PinHeader_1x04_P2.54mm_Vertical | 1 | TTL Connector
32 | J13 | PinHeader_1x02_P2.54mm_Vertical | 1 | LED Water Level
33 | J16 | TerminalBlock_Phoenix_PT-1,5-2-5.0-H_1x02_P5.00mm_Horizontal | 1 | Pomp3
34 | J20 | TerminalBlock_Phoenix_PT-1,5-2-5.0-H_1x02_P5.00mm_Horizontal | 1 | Luchtpomp
35 | J15 | BNC_Amphenol_B6252HB-NPP3G-50_Horizontal | 1 | Voedingsstoffen 1
36 | J3 | PinHeader_1x04_P2.54mm_Vertical | 1 | Height Mixer
37 | J12 | TerminalBlock_Phoenix_PT-1,5-2-5.0-H_1x02_P5.00mm_Horizontal | 1 | Pomp2
38 | J2 | PinHeader_1x04_P2.54mm_Vertical | 1 | Height Nutrients
39 | J19 | BNC_Amphenol_B6252HB-NPP3G-50_Horizontal | 1 | Voedingsstoffen 2
40 | Q1,Q3,Q6,Q4,Q2,Q5,Q7 | SOT-23 | 7 | BSS138
41 | D8,D9,D10,D7,D5,D6,D4 | D_0805_2012Metric_Pad1.15x1.40mm_HandSolder | 7 | 1N4148
42 | U5 | SOIC-28W_7.5x17.9mm_P1.27mm | 1 | MCP23017_SO
43 | C8 | CP_EIA-3528-12_Kemet-T_Pad1.50x2.35mm_HandSolder | 1 | 22u
44 | R10,R12 | R_0805_2012Metric_Pad1.20x1.40mm_HandSolder | 2 | 4.7k
45 | C9,C5 | C_0805_2012Metric_Pad1.18x1.45mm_HandSolder | 2 | 10u
46 | U4 | SOT-223-3_TabPin2 | 1 | AMS1117-3.3
47 | D3 | DIOM5226X290N | 1 | SK36A

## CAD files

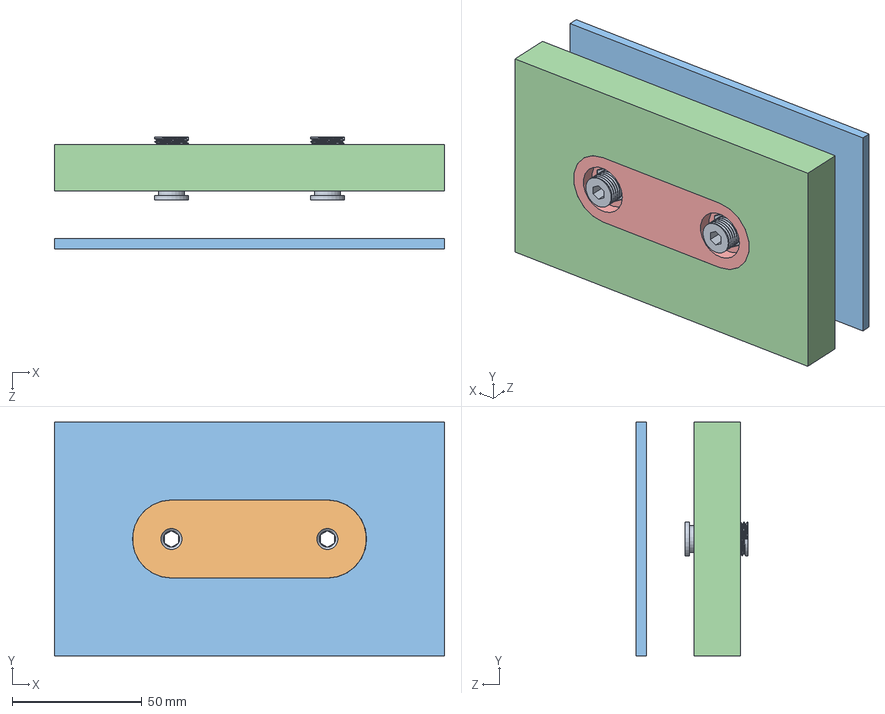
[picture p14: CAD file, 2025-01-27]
Water/3D-modellen/Common_Connector/3D-modellen/Common_Connector.SLDASM
150.0 x 90.0 x 43.0 mm
Common_Connector_F_Plate
Wall
PlantBox
Common_Connector_M_Plate
QuickConnect x 2

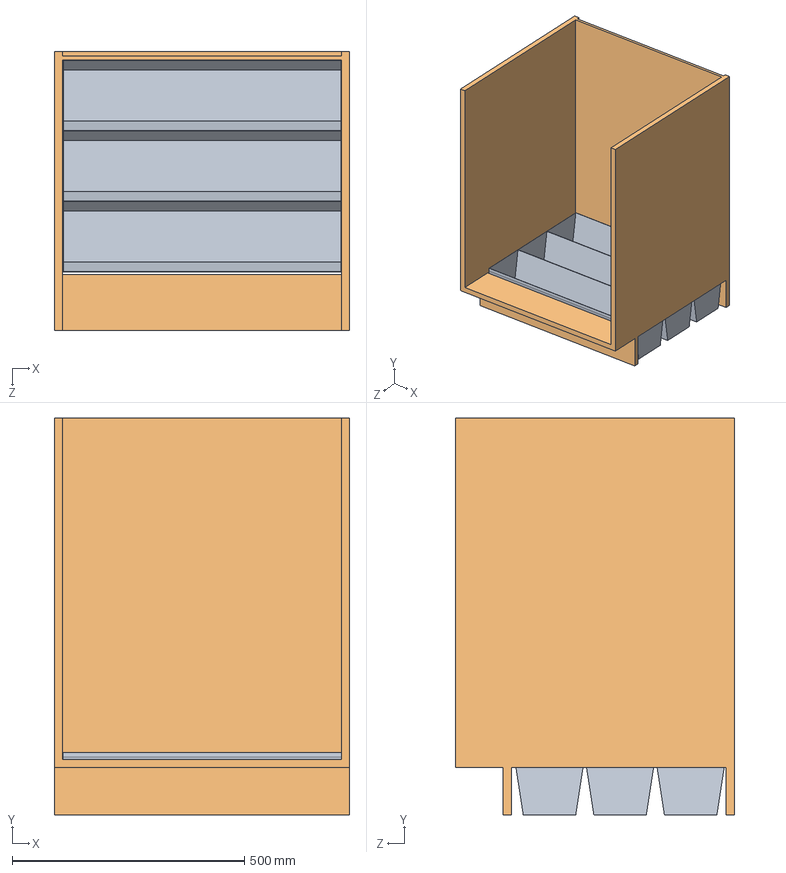
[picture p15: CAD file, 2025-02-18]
Water/3D-modellen/Ineengestoken_Kast.SLDASM
636.0 x 855.0 x 600.0 mm
Kast
Waterbak_Gevijld x 3

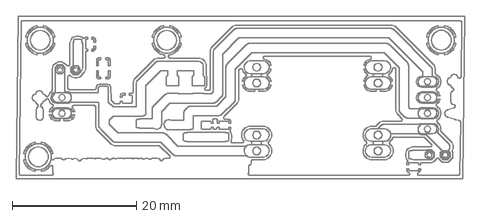
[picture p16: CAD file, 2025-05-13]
Licht/Powermeting/.dxf
72.1 x 26.0 mm

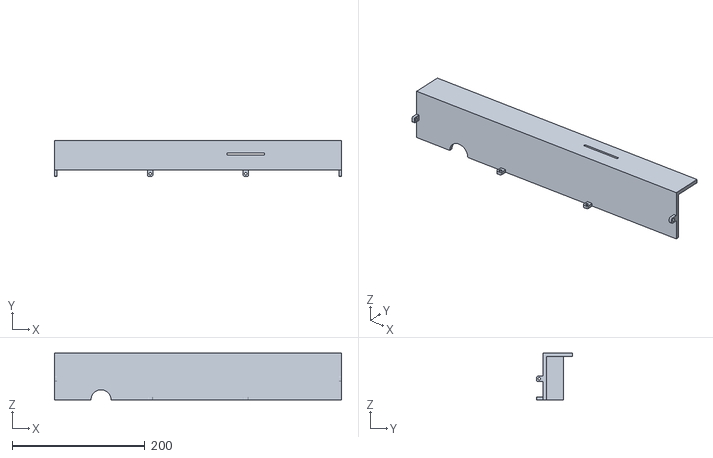
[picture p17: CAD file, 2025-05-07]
Plantenbak/3D-modellen/plantenbak.stl
432.0 x 54.0 x 70.0

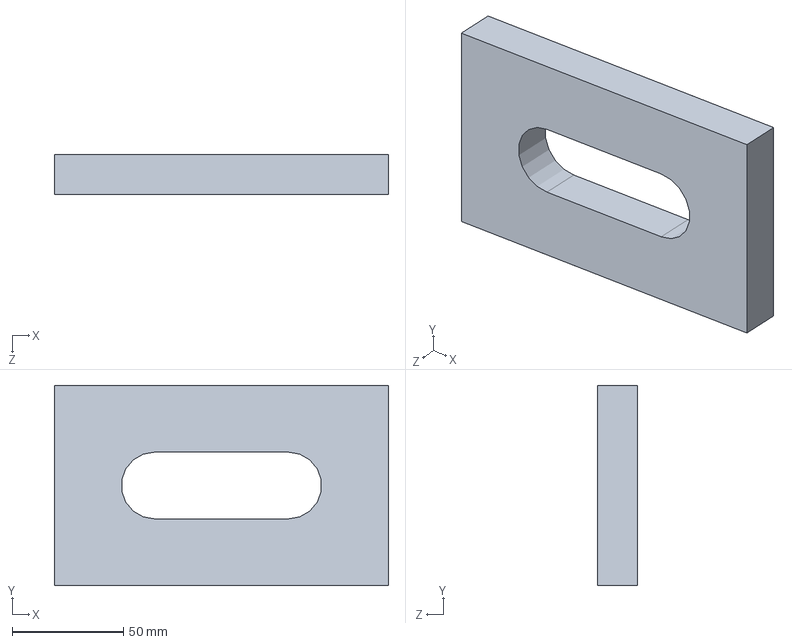
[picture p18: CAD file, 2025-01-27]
Water/3D-modellen/Common_Connector/3D-modellen/Wall.SLDPRT
150.0 x 90.0 x 18.0 mm

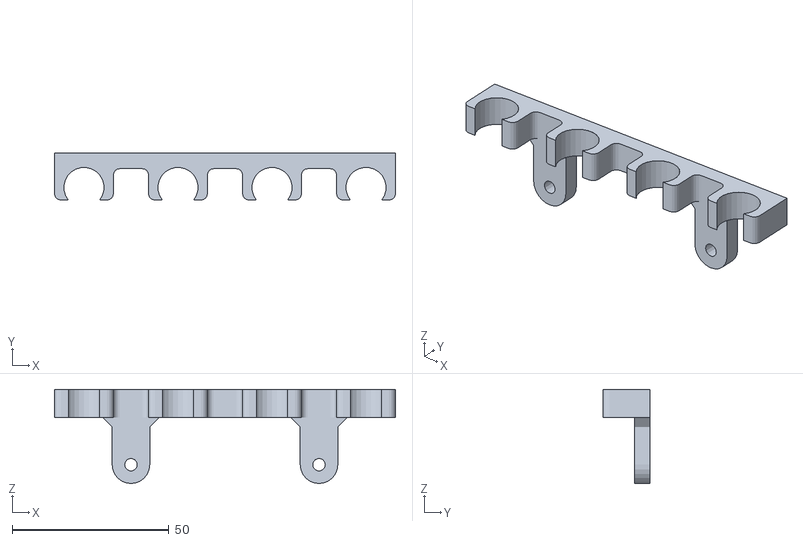
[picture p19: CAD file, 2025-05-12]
Water/3D-modellen/ProbeHouder.stl
108.8 x 15.0 x 30.0

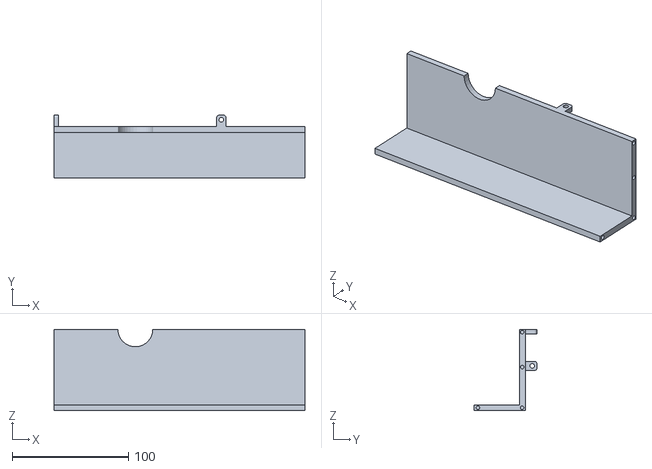
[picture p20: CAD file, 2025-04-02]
Plantenbak/3D-modellen/plantenbak_1.stl
216.0 x 54.0 x 70.0

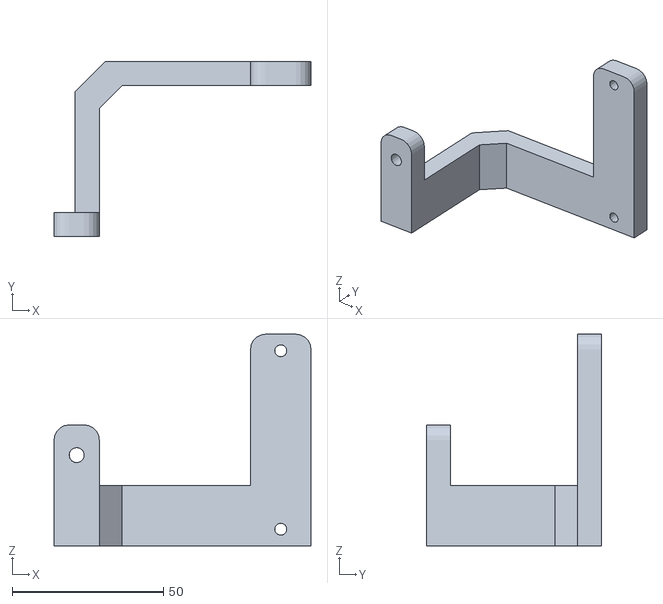
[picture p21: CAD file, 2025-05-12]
Water/3D-modellen/HoogtesensorHouder.stl
85.0 x 58.0 x 70.0

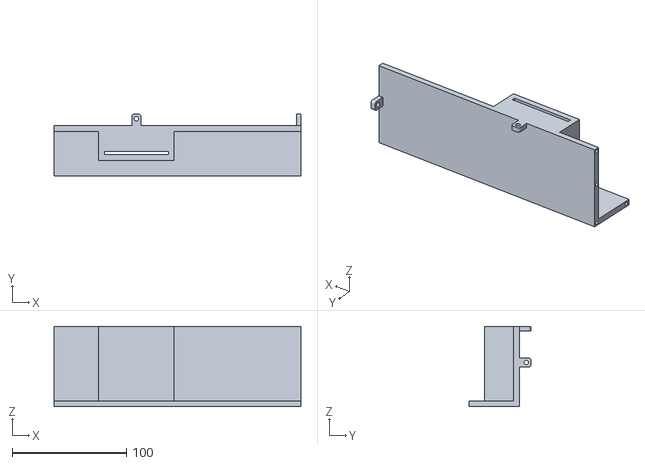
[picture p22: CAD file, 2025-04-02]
Plantenbak/3D-modellen/plantenbak_2.stl
216.0 x 54.0 x 70.0

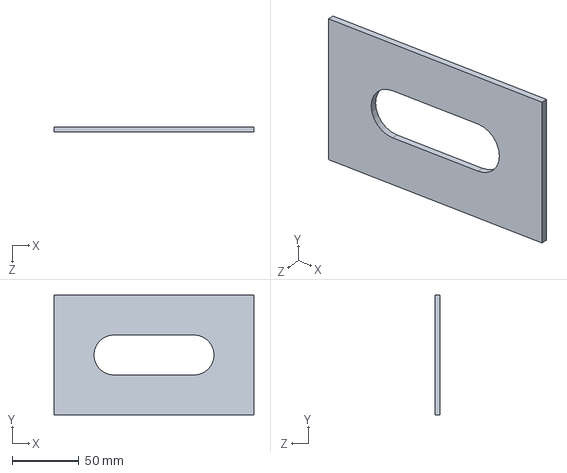
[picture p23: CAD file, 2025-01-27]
Water/3D-modellen/Common_Connector/3D-modellen/PlantBox.SLDPRT
150.0 x 90.0 x 4.00 mm

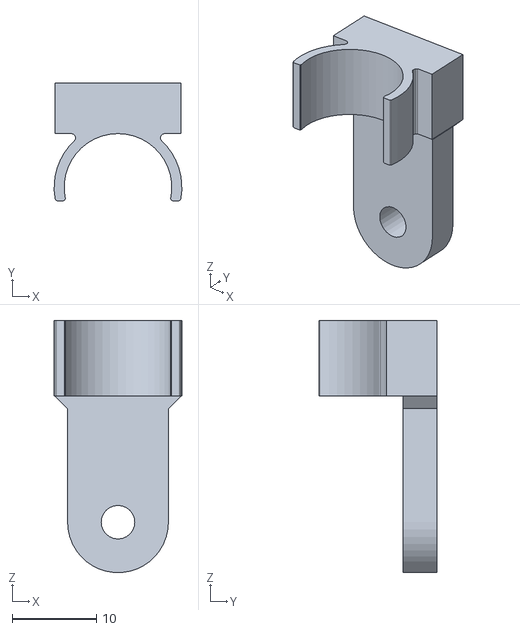
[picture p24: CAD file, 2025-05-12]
Water/3D-modellen/ProbeHouder - single.stl
15.2 x 14.0 x 30.0

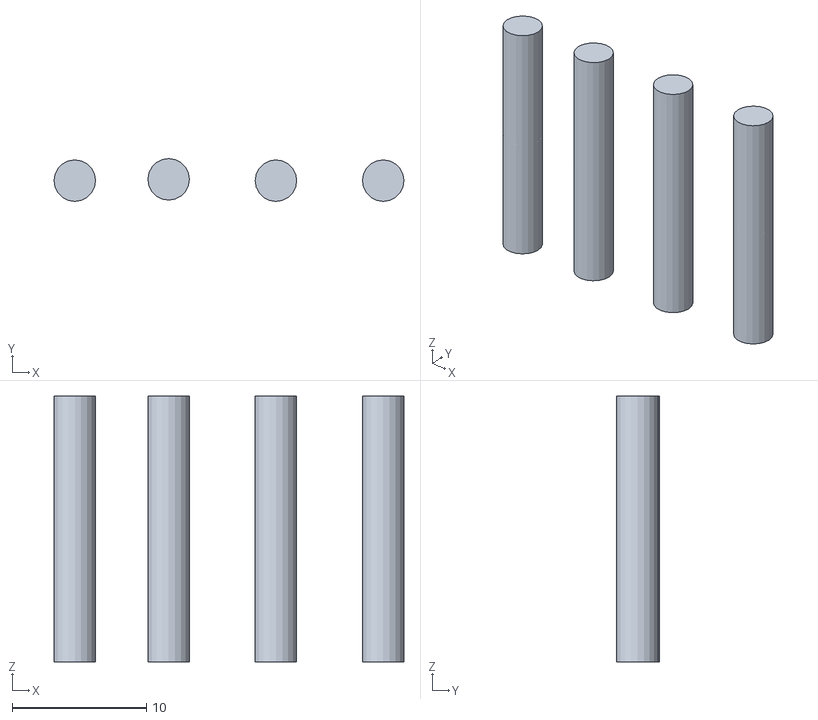
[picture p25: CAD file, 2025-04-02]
Plantenbak/3D-modellen/plantenbak_pins.stl
26.1 x 3.20 x 19.8

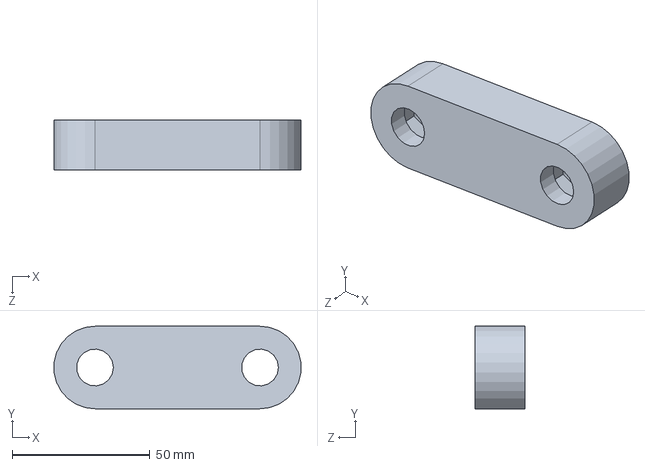
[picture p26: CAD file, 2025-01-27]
Water/3D-modellen/Common_Connector/3D-modellen/Common_Connector_F_Plate.SLDPRT
89.8 x 30.0 x 18.0 mm

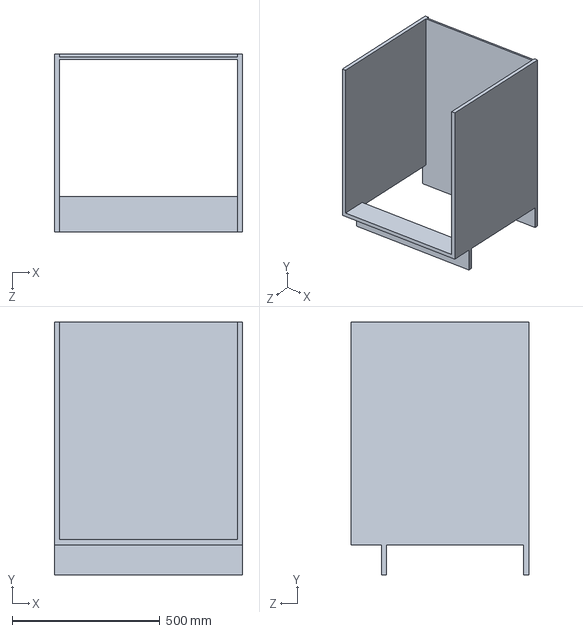
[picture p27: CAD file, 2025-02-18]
Water/3D-modellen/Kast.SLDPRT
636.0 x 855.0 x 600.0 mm

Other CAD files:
Water/3D-modellen/Watersysteem_Boven.SLDASM
Water/3D-modellen/Common_Connector/3D-modellen/QuickConnect.SLDPRT
Water/3D-modellen/Waterbak_Gevijld.SLDPRT
Water/3D-modellen/Common_Connector/3D-modellen/Common_Connector_M_Plate.SLDPRT
Water/3D-modellen/Common_Connector/3D-modellen/HoseBarb.SLDPRT
Water/3D-modellen/Magneetventiel.SLDPRT
Water/3D-modellen/VentielSupport_1.SLDPRT
Water/3D-modellen/Waterbak.SLDPRT

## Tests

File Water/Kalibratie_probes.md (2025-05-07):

# Chemie Kalibratievloeistoffen

We maken stockoplossingen met de volgende concentraties:

| Ion  | Calibration Salt | Desired Ion Concentration (g/l) | Desired Salt Concentration (g/l) | Measured Salt Concentration (g/l) | Actual Ion Concentration (g/l) |
|---|---|---|---|---|---|
| NO₃⁻ | NaNO₃ | 16 | 21.93 | 21.90 | 15.98 |
| Ca²⁺ | Ca(NO₃)₂4H₂O | 2 | 11.7845 | 11.786 | 2.00 |
| K⁺ | KOH | 2 | 2.8699 | 2.915 | 2.03 |

Om de kalibratieoplossingen te maken, voegen we gedestilleerd water toe aan de stockoplossingen om drie verschillende ionconcentraties te bereiken. Deze drie waarden bestrijken het verwachte bereik dat door de sensoren wordt gebruikt.

| Ion | Parts Stock Solution | Addition for High | Addition for Medium | Addition for Low |
|---|---|---|---|---|
| NO₃⁻  | 1 part | 9 parts H₂O | 15.67 parts H₂O | 19 parts H₂O |
| Ca²⁺  | 1 part | 4 parts H₂O | 9 parts H₂O | 19 parts H₂O |
| K⁺ | 1 part | 4 parts H₂O | 9 parts H₂O | 19 parts H₂O |

### Absolute Hoeveelheden voor Kalibratievloeistof

| Ion | High (ml stock + ml H₂O) | Medium (ml stock + ml H₂O) | Low (ml stock + ml H₂O) |
|---|---|---|---|
| NO₃⁻  | 10ml stock + 90ml H₂O  | 6ml stock + 94ml H₂O | 10ml stock + 190ml H₂O  |
| Ca²⁺  | 20ml stock + 80ml H₂O  | 10ml stock + 90ml H₂O | 10ml stock + 190ml H₂O  |
| K⁺ | 20ml stock + 80ml H₂O  | 10ml stock + 90ml H₂O | 10ml stock + 190ml H₂O  |

Dit komt overeen met de onderstaande concentraties. Hiermee kalibreren we onze sensoren zodra de PCB is gemaakt.

| Ion | Calibration Salt | Low (mg/l) | Medium (mg/l) | High (mg/l) |
|---|---|---|---|---|
| NO₃⁻  | NaNO₃ | 799 | 959 | 1598 |
| Ca²⁺  | Ca(NO₃)₂4H₂O | 100 | 200 | 400 |
| K⁺ | KOH | 102 | 203 | 406 |

### pH-waarden per kalibratievloeistof

| Ion | Stock | High  | Medium | Low  |
|---|---|---|---|---|
| NO₃⁻  | 7 | 7 | 7 | 7 |
| Ca²⁺  | 6-7 | 6-7 | 6-7 | 6-7  |
| K⁺ | 12.7  | 12.0  | 11.7 | 11.4 |

## Kalibratie per Sensor

De sensoren werden uitgelezen na enige tijd ondergedompeld te zijn in de kalibratievloeistoffen. We maten pas deze uitgansspanning nadat de meetwaarde gestabiliseerd werd. Deze kalibraties werden twee keer uitgevoerd (met een week tussen beide kalibraties).

### Kalibratie van de K⁺-sensor

| K⁺ Concentratie (mg/l) | Gemeten Spanning kalibratie 1 (V) | Gemeten Spanning kalibratie 2 (V) |
|---|---|---|
| 406 | 0.102 | 0.118
| 203 | 0.093 |0.106
| 102 | 0.083 |0.091

<p float="left">
  <p align="center">
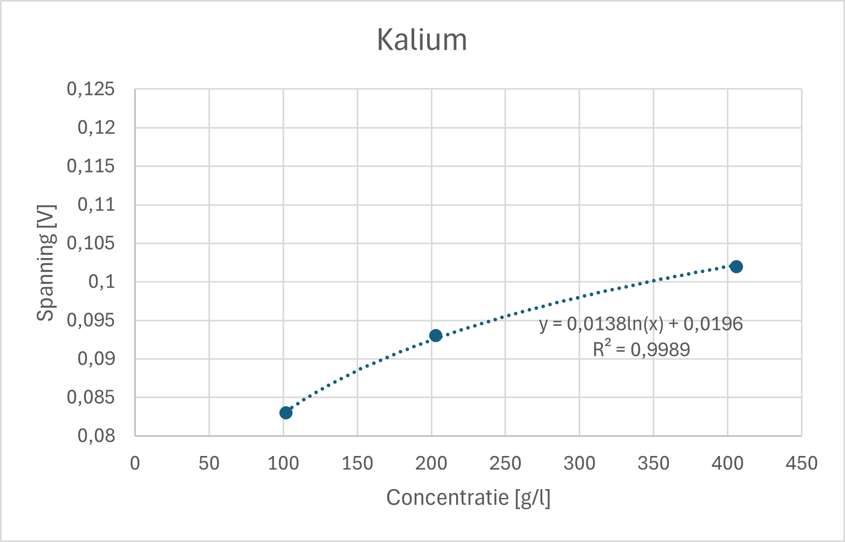
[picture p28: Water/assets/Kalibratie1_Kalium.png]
    <br><sub>Kalibratie 1</sub>
  </p>
  <p align="center">
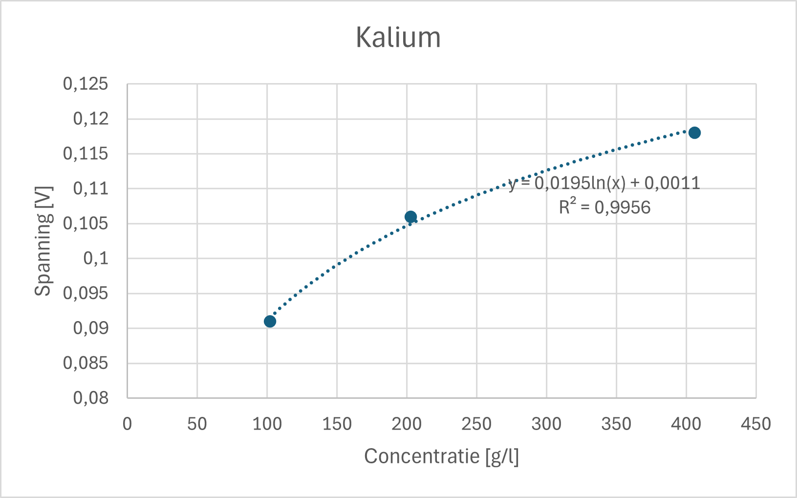
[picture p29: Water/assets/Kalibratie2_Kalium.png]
    <br><sub>Kalibratie 2</sub>
  </p>
</p>

Na zo'n tien tot twintig seconden waren de metingen stabiel. We verkrijgen een nagenoeg perfect logaritmisch verband na het uitvoeren van regressie op deze meetwaarden.

### Kalibratie van de Ca²⁺-sensor

| Ca²⁺ Concentratie (mg/l) | Gemeten Spanning kalibratie 1 (V) | Gemeten Spanning kalibratie 2 (V) |
|---|---|---|
| 400 | 0.044 | 0.033
| 200 | 0.038 | 0.028
| 100 | 0.032 | 0.023

<p float="left">
  <p align="center">
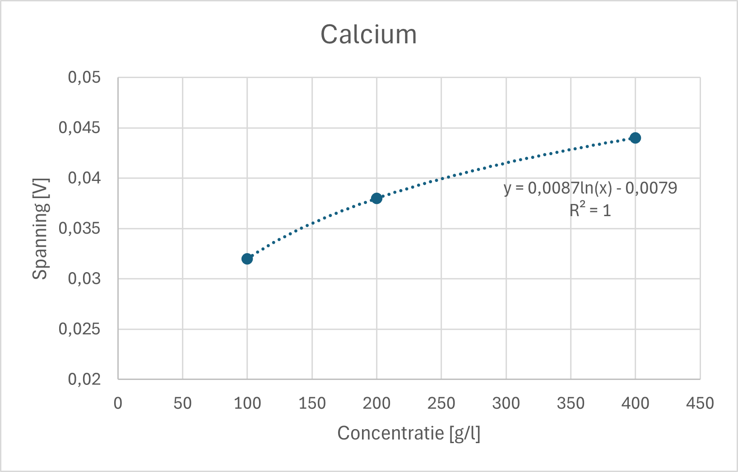
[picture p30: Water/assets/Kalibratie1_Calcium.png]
    <br><sub>Kalibratie 1</sub>
  </p>
  <p align="center">
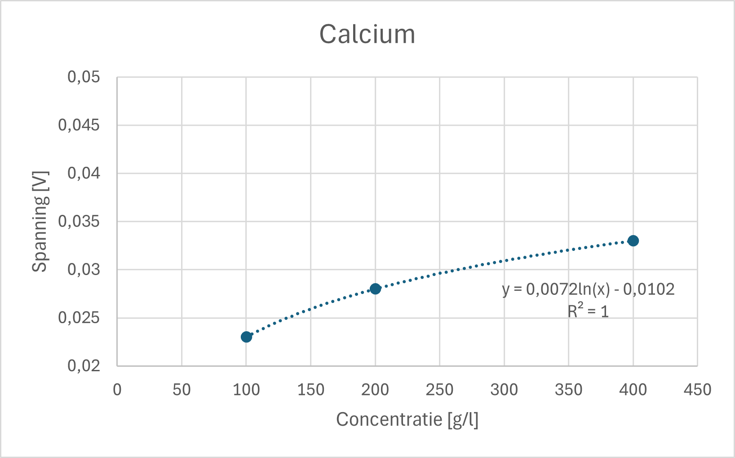
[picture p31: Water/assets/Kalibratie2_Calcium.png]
    <br><sub>Kalibratie 2</sub>
  </p>
</p>

Na zo'n tien seconden waren de metingen stabiel. We verkrijgen een nagenoeg perfect logaritmisch verband na het uitvoeren van regressie op deze meetwaarden.

### Kalibratie van de NO₃⁻-sensor

| NO₃⁻ Concentratie (mg/l) | Gemeten Spanning kalibratie 1 (V) | Gemeten Spanning kalibratie 2 (V) |
|---|---|---|
| 1598 | 0.027 | 0.0465
| 959 | 0.013 | 0.0325
| 799 | 0.027 | 0.018

<p float="left">
  <p align="center">
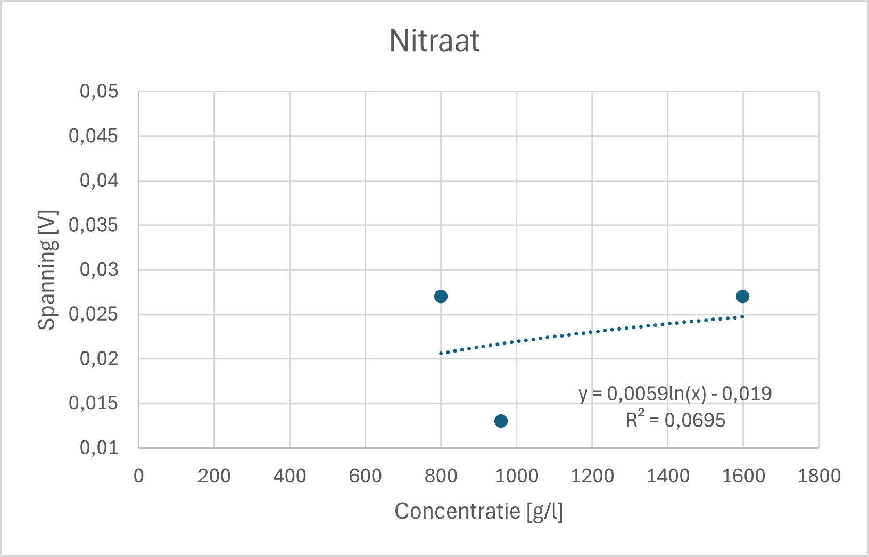
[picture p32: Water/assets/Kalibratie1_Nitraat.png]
    <br><sub>Kalibratie 1</sub>
  </p>
  <p align="center">
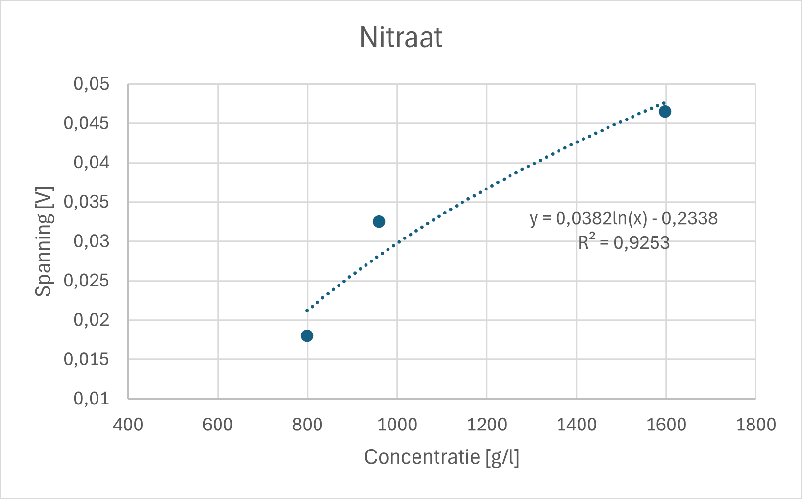
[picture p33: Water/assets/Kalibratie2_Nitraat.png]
    <br><sub>Kalibratie 2</sub>
  </p>
</p>

Bij de eerste meting verkregen we geen verband tussen de meetwaarden. Bij de tweede meting was er wel een verband te vinden, maar de meetwaarden waren opmerkelijk laag vergeleken met de kalibraties die men vorig jaar uitvoerde.

### Kalibratie van de pH-sensor

| pH-waarde | Gemeten Spanning (V) |
|---|---|
| 7 | 2.24
| 11.4 | 1.92
| 12 | 1.78

<p float="left">
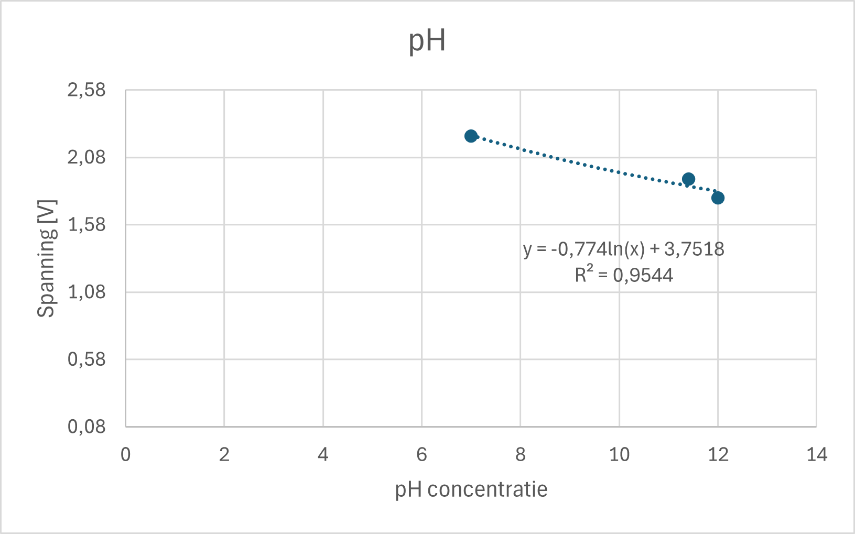
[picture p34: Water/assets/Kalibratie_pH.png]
  
</p>

De pH-probe werd gekalibreerd met behulp van de eerder gemaakte kalibratievloeistoffen.

## Uitmeten van kraantjeswater

In onze verticale farm zullen we gebruik maken van kraantjewater (verdund met de voedingsstoffen). We maten dit water uit en vergeleken de waarden met een rapport van Farys [1].

In kraantjeswater meten we volgende hoeveelheden:

| Voedingsstof | Concentratie | Verwachte waarde [1] |
|---|---|---|
| Nitraat | 2100 mg/l | 10.7 mg/l |
| Kalium | 260 mg/l | 4.5 mg/l |
| Calcium | 120 mg/l | 86mg/l |
| pH | 6.1 | 7.8 |

Voor beide kalibraties kwamen we onrealistische waarden uit bij de nitraat- en kaliummetingen. De verhoogde waarde van calcium is realistisch, dit kan te wijten zijn aan verkalkte leidingen. De pH is ook redelijk neutraal en beschouwen we als aanvaardbaar.

[1] Farys, “Watersamenstelling en hardheid in jouw gemeente,” Farys.be. [Online]. Beschikbaar: https://www.farys.be/nl/watersamenstelling-en-hardheid-in-jouw-gemeente. [Geraadpleegd: 7-mei-2025]

## Uitmeten van de voedingsstoffen

De voedingsstoffen worden kant-en-klaar aangekocht in een tuincentrum. Dit ligt in lijn met het doel om de verticale farm commercieel op de markt te brengen, de voedingsstoffen zijn voor iedereen verkrijgbaar en kosten niet veel.

Op basis van de aanbevolen hoeveelheden voedingsstoffen (1 dop per 8l) en de grootte van de reservoirs (8l) kozen we ervoor om volgende aanbeveling te maken voor de gebruiker: "Wanneer u het voedingsstoffenreservoir bijvult dient u 1 dopje voedingsstoffen per vol reservoir toe te voegen".
De voedingsstoffen worden succesvol gemixt met het water door het luchtpompje.

Na het toevoegen van deze concentratie meten we volgende concentraties op:

| Voedingsstof | Concentratie |
|---|---|
| Nitraat | 2600 mg/l |
| Kalium | 410 mg/l |
| Calcium | 26 mg/l |
| pH | 4.7 |

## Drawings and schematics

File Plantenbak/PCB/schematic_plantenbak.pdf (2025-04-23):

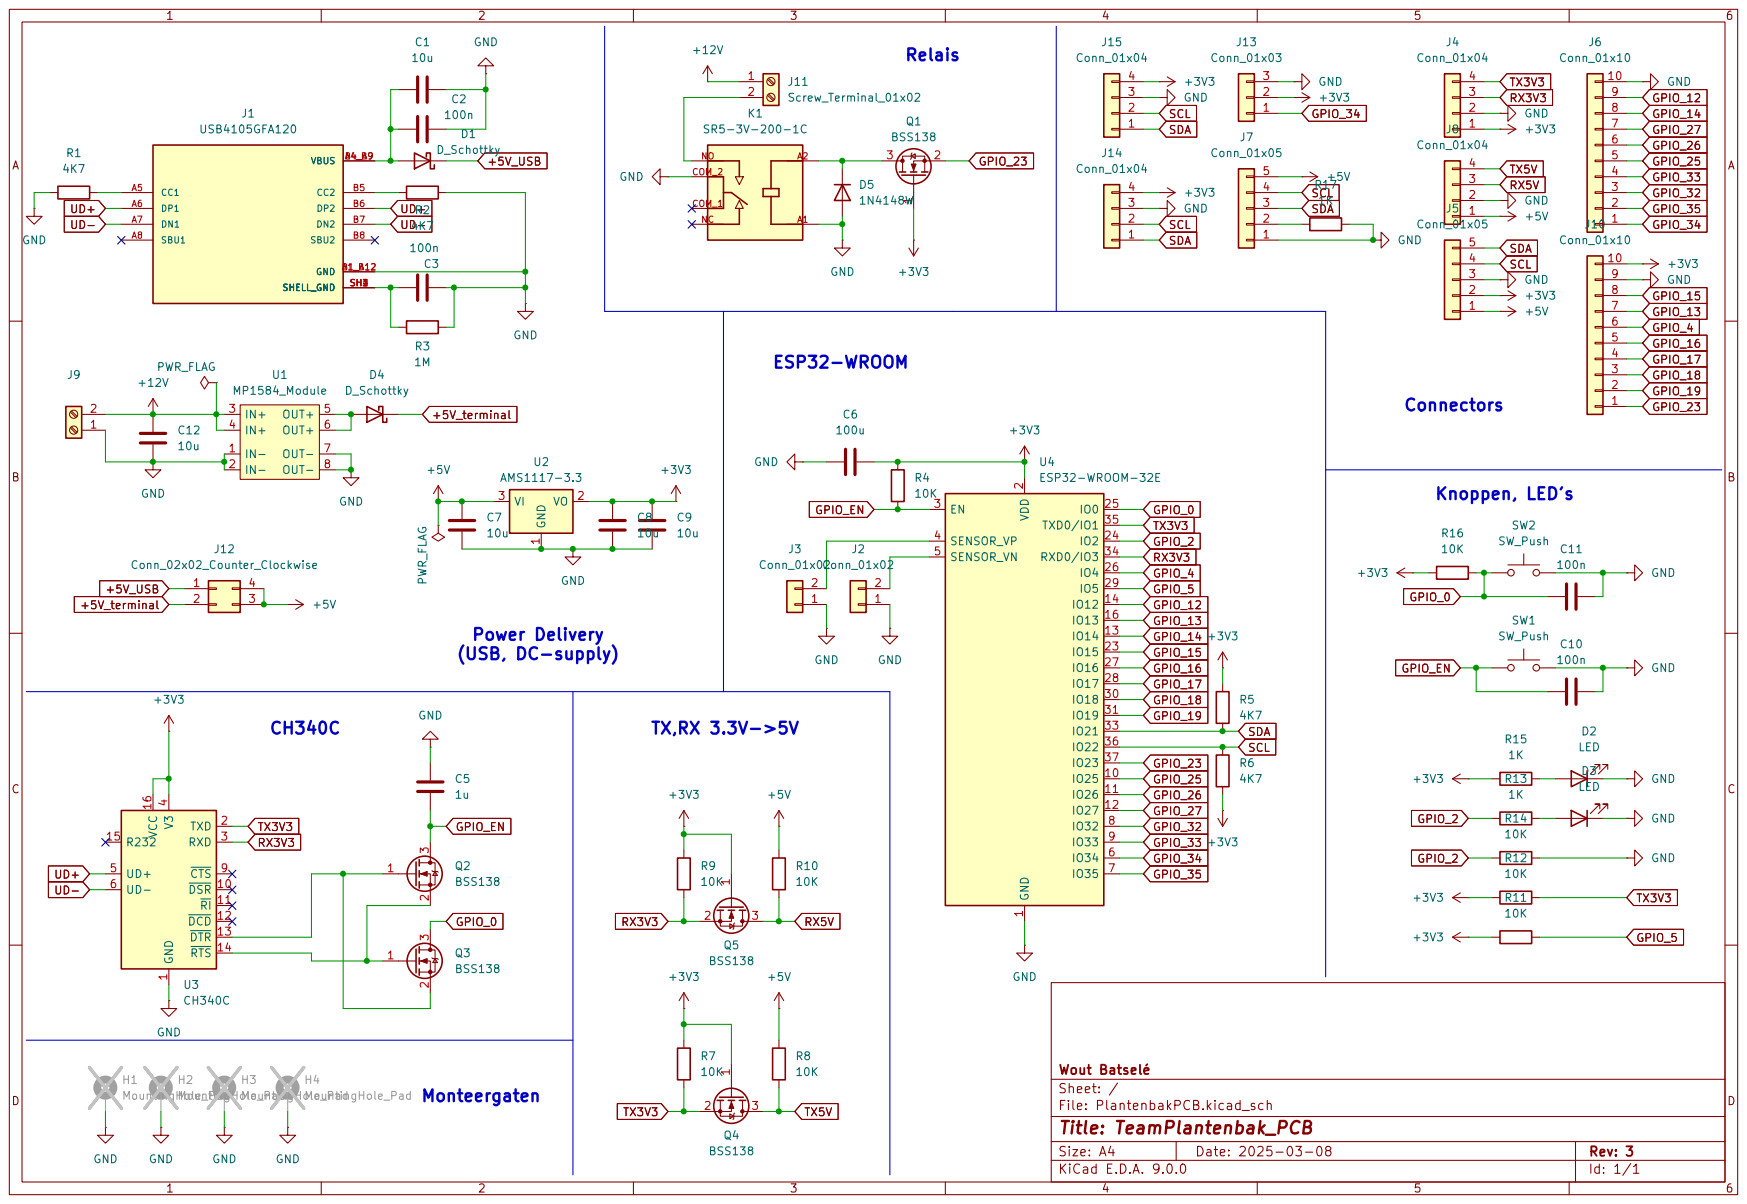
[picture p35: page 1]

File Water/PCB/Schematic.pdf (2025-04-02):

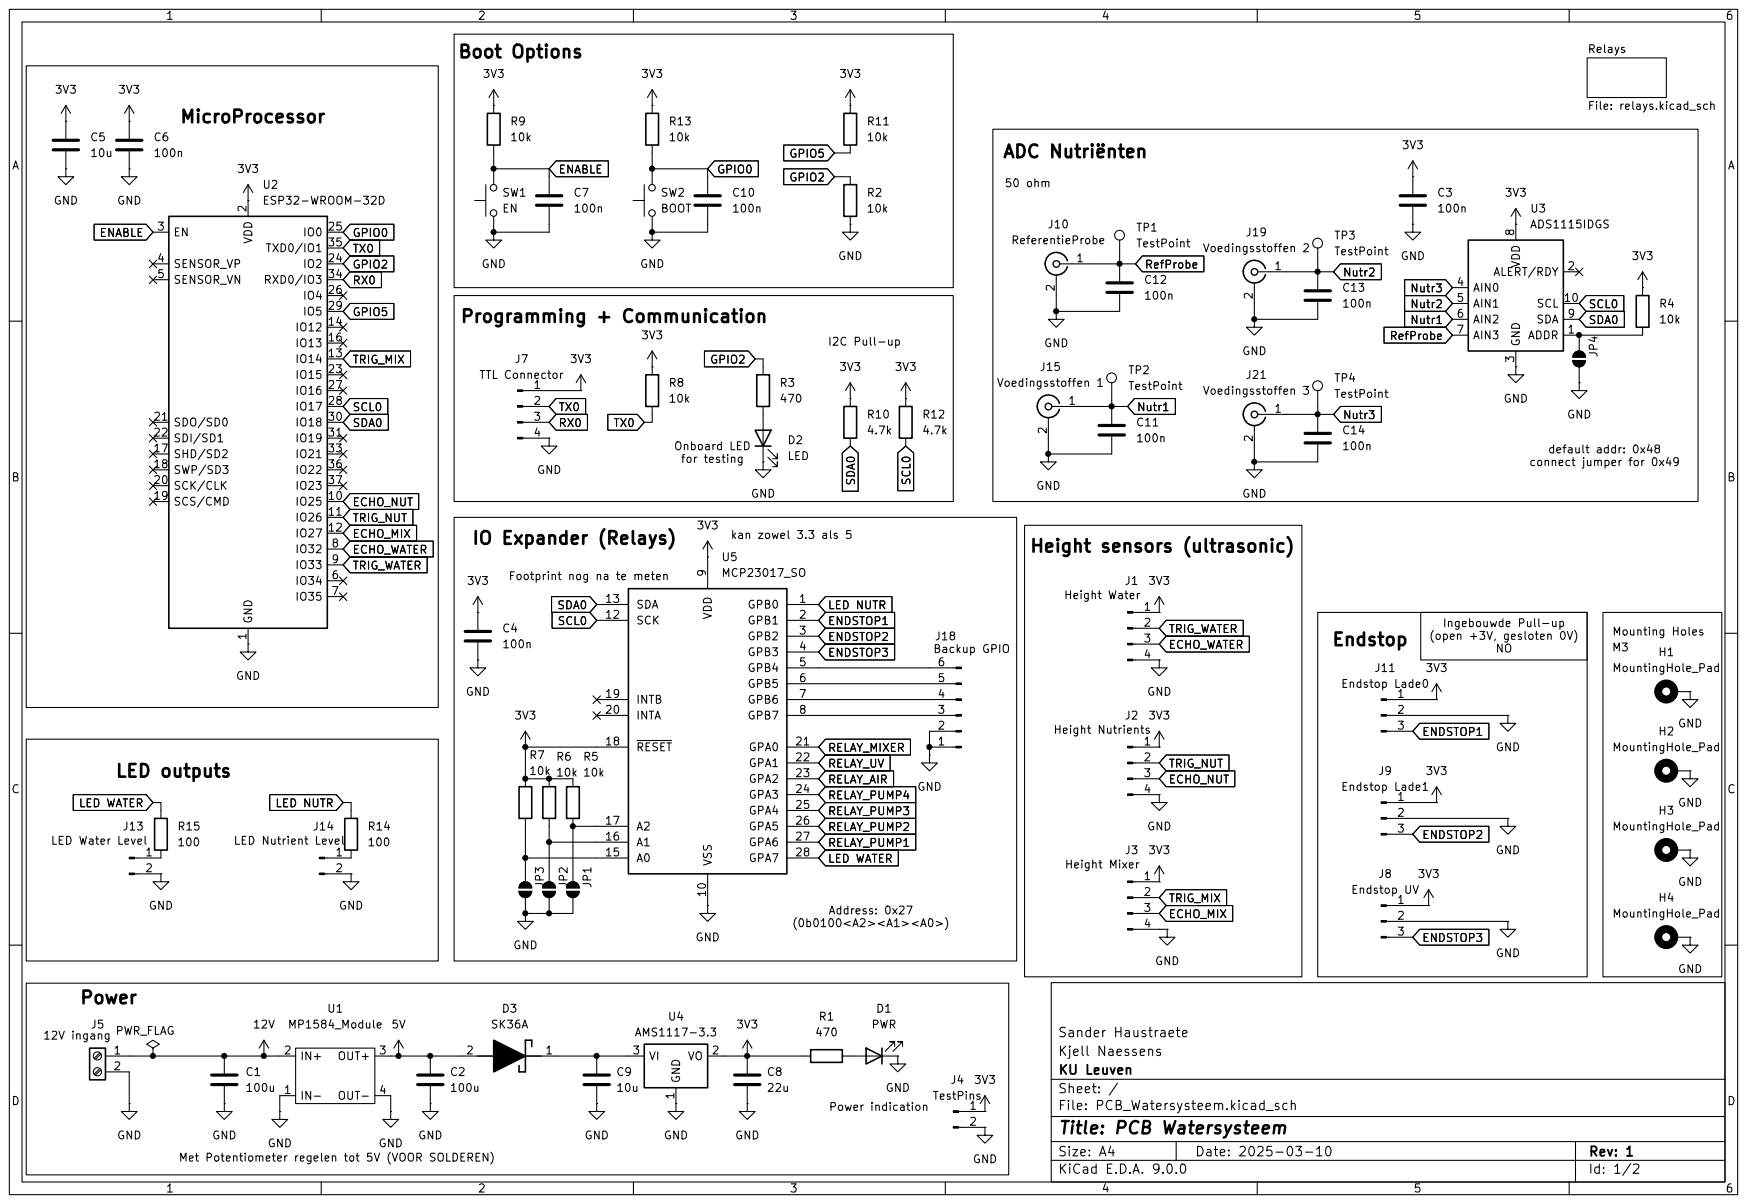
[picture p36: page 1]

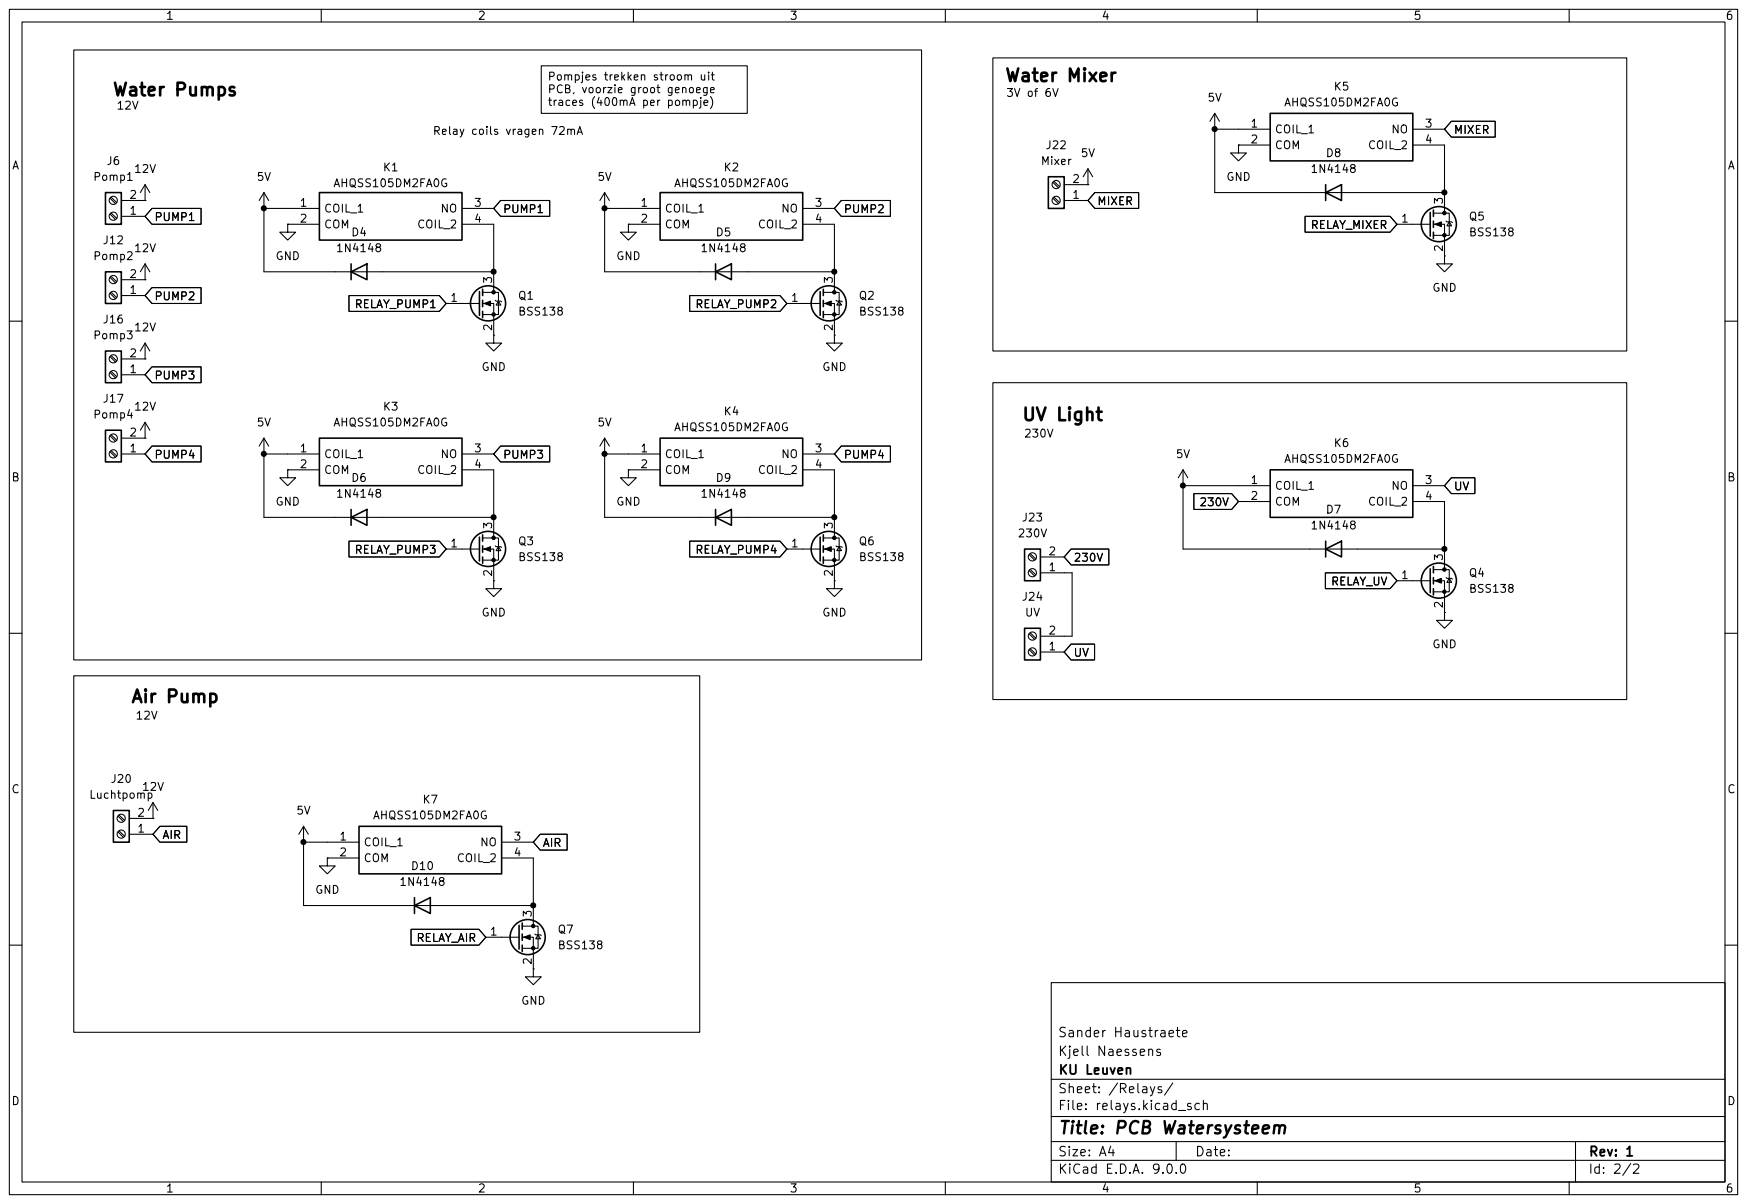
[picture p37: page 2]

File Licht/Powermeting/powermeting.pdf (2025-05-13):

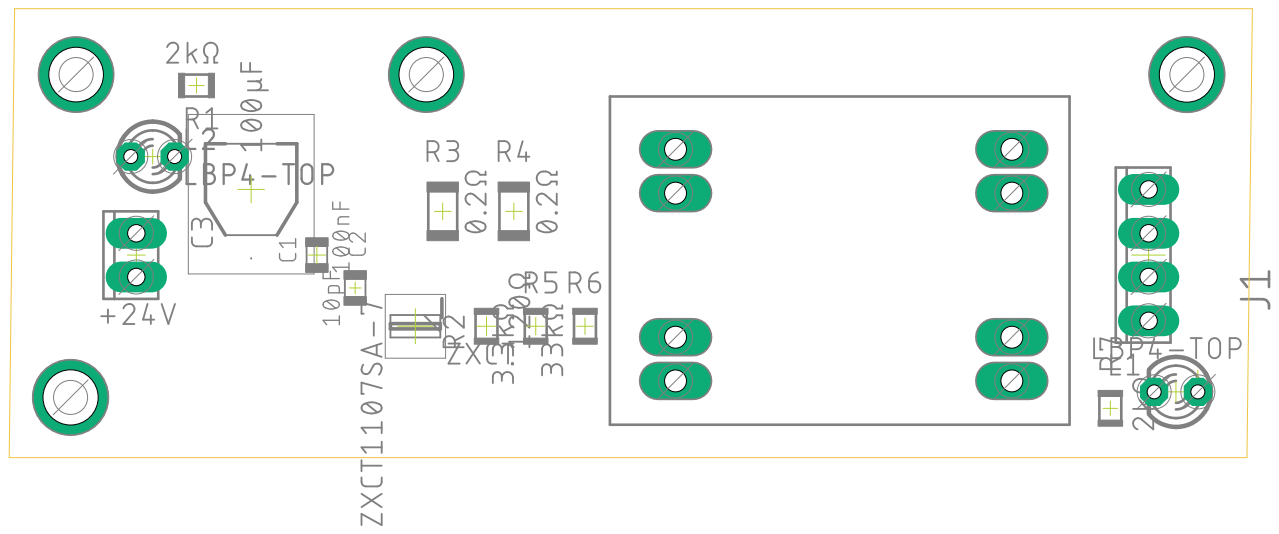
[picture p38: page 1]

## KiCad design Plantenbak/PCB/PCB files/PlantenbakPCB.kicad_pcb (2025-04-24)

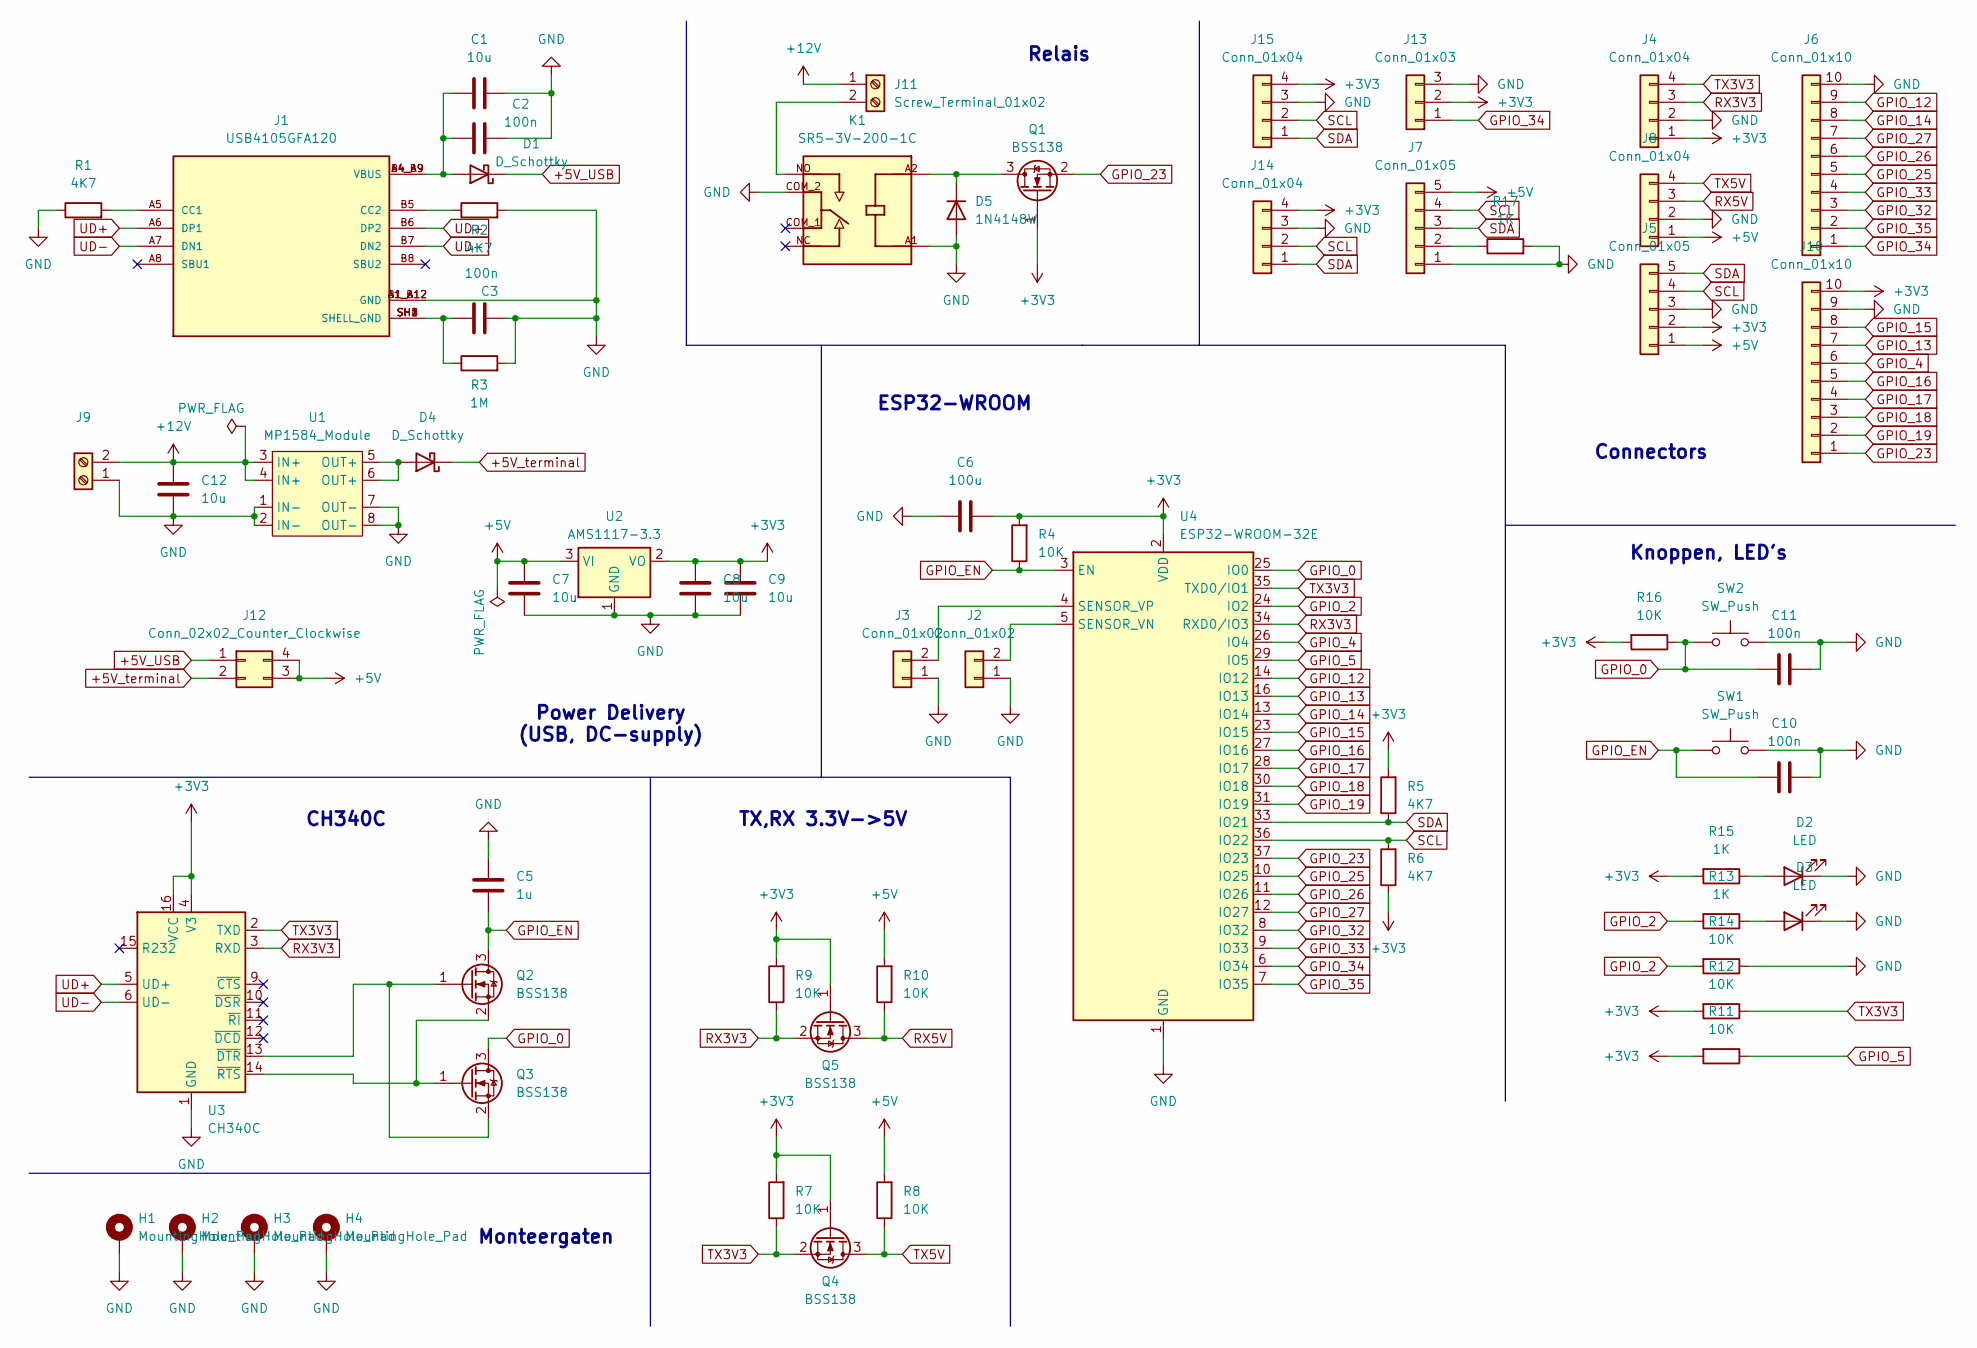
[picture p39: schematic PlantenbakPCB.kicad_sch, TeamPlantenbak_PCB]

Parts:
C1, C7, C8, C9, C12: 10u; C_0805_2012Metric_Pad1.18x1.45mm_HandSolder
C2, C3, C10, C11: 100n; C_0805_2012Metric_Pad1.18x1.45mm_HandSolder
C5: 1u; C_0805_2012Metric_Pad1.18x1.45mm_HandSolder
C6: 100u; C_0805_2012Metric_Pad1.18x1.45mm_HandSolder
D1, D4: D_Schottky; D_SOD-323_HandSoldering
D2, D3: LED; LED_0805_2012Metric_Pad1.15x1.40mm_HandSolder
D5: 1N4148W; D_SOD-123
H1, H2, H3, H4: MountingHole_Pad; MountingHole_3.2mm_M3_Pad_TopBottom
J1: USB4105GFA120; GCT_USB4105GFA120; PARTREV B3
J2, J3: Conn_01x02; PinHeader_1x02_P2.54mm_Vertical
J4, J8, J14, J15: Conn_01x04; PinHeader_1x04_P2.54mm_Vertical
J5, J7: Conn_01x05; PinHeader_1x05_P2.54mm_Vertical
J6, J10: Conn_01x10; PinHeader_1x10_P2.54mm_Vertical
J9, J11: Screw_Terminal_01x02; TerminalBlock_Phoenix_MKDS-1,5-2-5.08_1x02_P5.08mm_Horizont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
J12: Conn_02x02_Counter_Clockwise; PinHeader_2x02_P2.54mm_Vertical
J13: Conn_01x03; PinHeader_1x03_P2.54mm_Vertical
K1: SR5-3V-200-1C; RELAY_SR5-3V-200-1C; PARTREV 1.01
Q1, Q2, Q3, Q4, Q5: BSS138; SOT-23
R1, R2, R5, R6: 4K7; R_0805_2012Metric_Pad1.20x1.40mm_HandSolder
R3: 1M; R_0805_2012Metric_Pad1.20x1.40mm_HandSolder
R4, R7, R8, R9, R10, R11, R12, R14, R16: 10K; R_0805_2012Metric_Pad1.20x1.40mm_HandSolder
R13, R15, R17: 1K; R_0805_2012Metric_Pad1.20x1.40mm_HandSolder
SW1, SW2: SW_Push; 434111043826
U1: MP1584_Module
U2: AMS1117-3.3; SOT-223-3_TabPin2
U3: CH340C; SOIC-16_3.9x9.9mm_P1.27mm
U4: ESP32-WROOM-32E

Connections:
+3V3: C6.2, C8.2, C9.1, J4.1, J5.2, J10.10, J13.2, J14.4, J15.4, Q1.1 (G), Q4.1 (G), Q5.1 (G), R4.2, R5.2, R6.1, R7.2, R9.2, R11.2, R12.2, R15.2, R16.2, U2.2 (VO), U3.4 (V3), U3.16 (VCC), U4.2 (VDD)
+5V: C7.2, J5.1, J7.5, J8.1, J12.3, J12.4, R8.2, R10.2, U2.3 (VI)
+5V_USB: D1.1 (K), J12.1
+5V_terminal: D4.1 (K), J12.2
+12V: C12.2, J9.2, J11.1, U1.3 (IN+), U1.4 (IN+)
GND: C1.2, C2.1, C3.2, C5.2, C6.1, C7.1, C8.1, C9.2, C10.2, C11.2, C12.1, D2.1 (K), D3.1 (K), D5.2 (A), H1.1, H2.1, H3.1, H4.1, J1.A1_B12 (GND), J1.B1_A12 (GND), J2.1, J3.1, J4.2, J5.3, J6.10, J7.1, J8.2, J9.1, J10.9, J13.3, J14.3, J15.3, K1.A1, K1.COM_2, R1.1, R2.2, R3.2, R14.1, R17.2, SW1.2, SW2.2, U1.1 (IN-), U1.2 (IN-), U1.7 (OUT-), U1.8 (OUT-), U2.1 (GND), U3.1 (GND), U4.1 (GND), U4.15 (GND), U4.38 (GND), U4.39 (GND)
GPIO_0: C11.1, Q3.3 (D), R16.1, SW2.1, U4.25 (IO0)
GPIO_2: R13.2, R14.2, U4.24 (IO2)
GPIO_4: J10.6, U4.26 (IO4)
GPIO_5: R11.1, U4.29 (IO5)
GPIO_12: J6.9, U4.14 (IO12)
GPIO_13: J10.7, U4.16 (IO13)
GPIO_14: J6.8, U4.13 (IO14)
GPIO_15: J10.8, U4.23 (IO15)
GPIO_16: J10.5, U4.27 (IO16)
GPIO_17: J10.4, U4.28 (IO17)
GPIO_18: J10.3, U4.30 (IO18)
GPIO_19: J10.2, U4.31 (IO19)
GPIO_23: J10.1, Q1.2 (S), U4.37 (IO23)
GPIO_25: J6.5, U4.10 (IO25)
GPIO_26: J6.6, U4.11 (IO26)
GPIO_27: J6.7, U4.12 (IO27)
GPIO_32: J6.3, U4.8 (IO32)
GPIO_33: J6.4, U4.9 (IO33)
GPIO_34: J6.1, J13.1, U4.6 (IO34)
GPIO_35: J6.2, U4.7 (IO35)
GPIO_EN: C5.1, C10.1, Q2.3 (D), R4.1, SW1.1, U4.3 (EN)
unnamed: C3.1, J1.SH1 (SHELL_GND), J1.SH2 (SHELL_GND), J1.SH3 (SHELL_GND), J1.SH4 (SHELL_GND), R3.1
unnamed: C1.1, C2.2, D1.2 (A), J1.A4_B9 (VBUS), J1.B4_A9 (VBUS)
unnamed: D2.2 (A), R15.1
unnamed: D3.2 (A), R13.1
unnamed: D4.2 (A), U1.5 (OUT+), U1.6 (OUT+)
unnamed: D5.1 (K), K1.A2, Q1.3 (D)
unnamed: J1.A5 (CC1), R1.2
unnamed: J1.B5 (CC2), R2.1
unnamed: J2.2, U4.5 (SENSOR_VN)
unnamed: J3.2, U4.4 (SENSOR_VP)
unnamed: J7.2, R17.1
unnamed: J11.2, K1.NO
unnamed: Q2.1 (G), Q3.2 (S), U3.13 (~DTR)
unnamed: Q2.2 (S), Q3.1 (G), U3.14 (~RTS)
RX3V3: J4.3, Q5.2 (S), R9.1, U3.3 (RXD), U4.34 (RXD0/IO3)
RX5V: J8.3, Q5.3 (D), R10.1
SCL: J5.4, J7.4, J14.2, J15.2, R6.2, U4.36 (IO22)
SDA: J5.5, J7.3, J14.1, J15.1, R5.1, U4.33 (IO21)
TX3V3: J4.4, Q4.2 (S), R7.1, R12.1, U3.2 (TXD), U4.35 (TXD0/IO1)
TX5V: J8.4, Q4.3 (D), R8.1
UD+: J1.A6 (DP1), J1.B6 (DP2), U3.5 (UD+)
UD-: J1.A7 (DN1), J1.B7 (DN2), U3.6 (UD-)

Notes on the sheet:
Knoppen, LED's
TX,RX 3.3V->5V
CH340C
Connectors
Monteergaten
Relais
Power Delivery (USB, DC-supply)
ESP32-WROOM

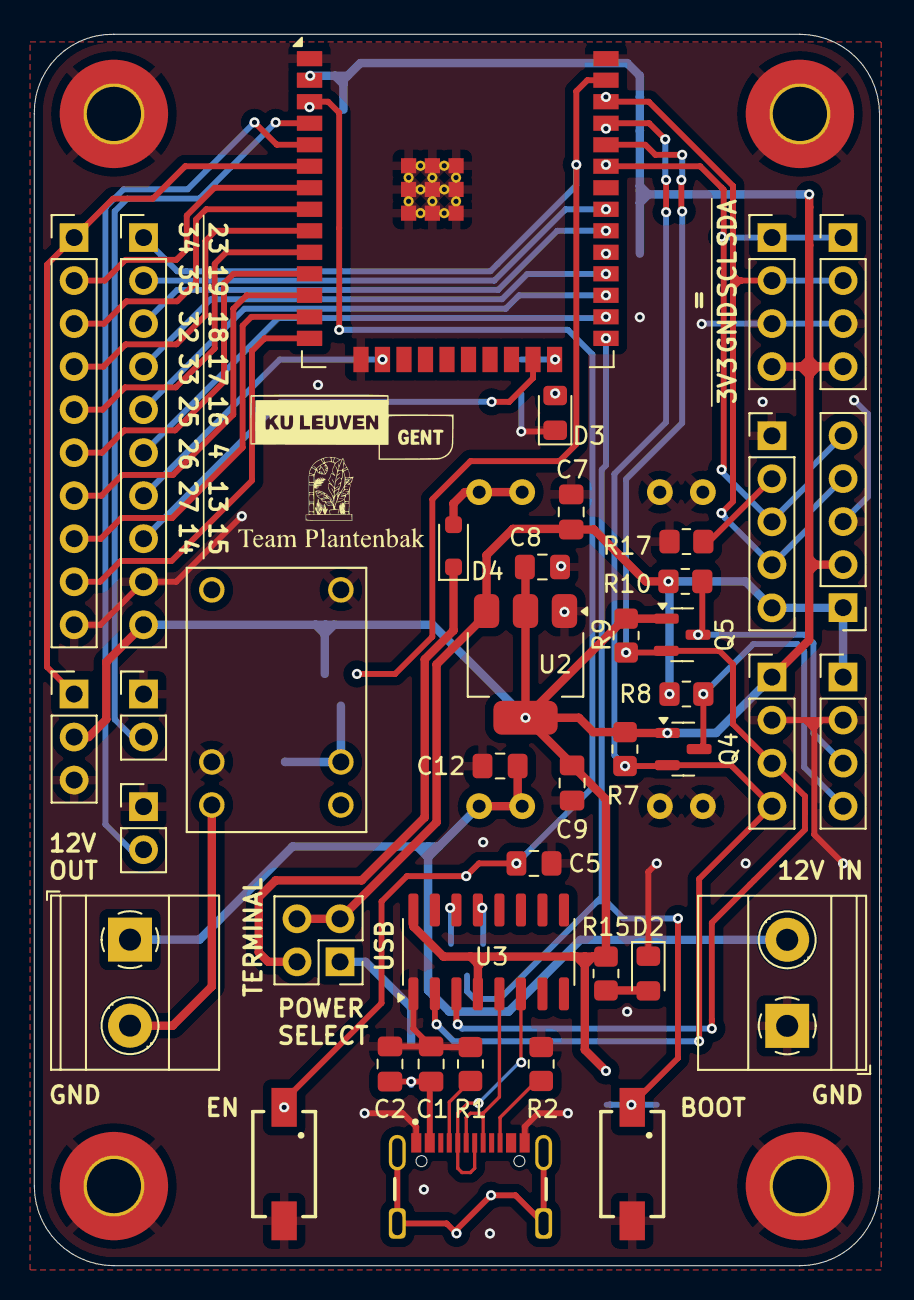
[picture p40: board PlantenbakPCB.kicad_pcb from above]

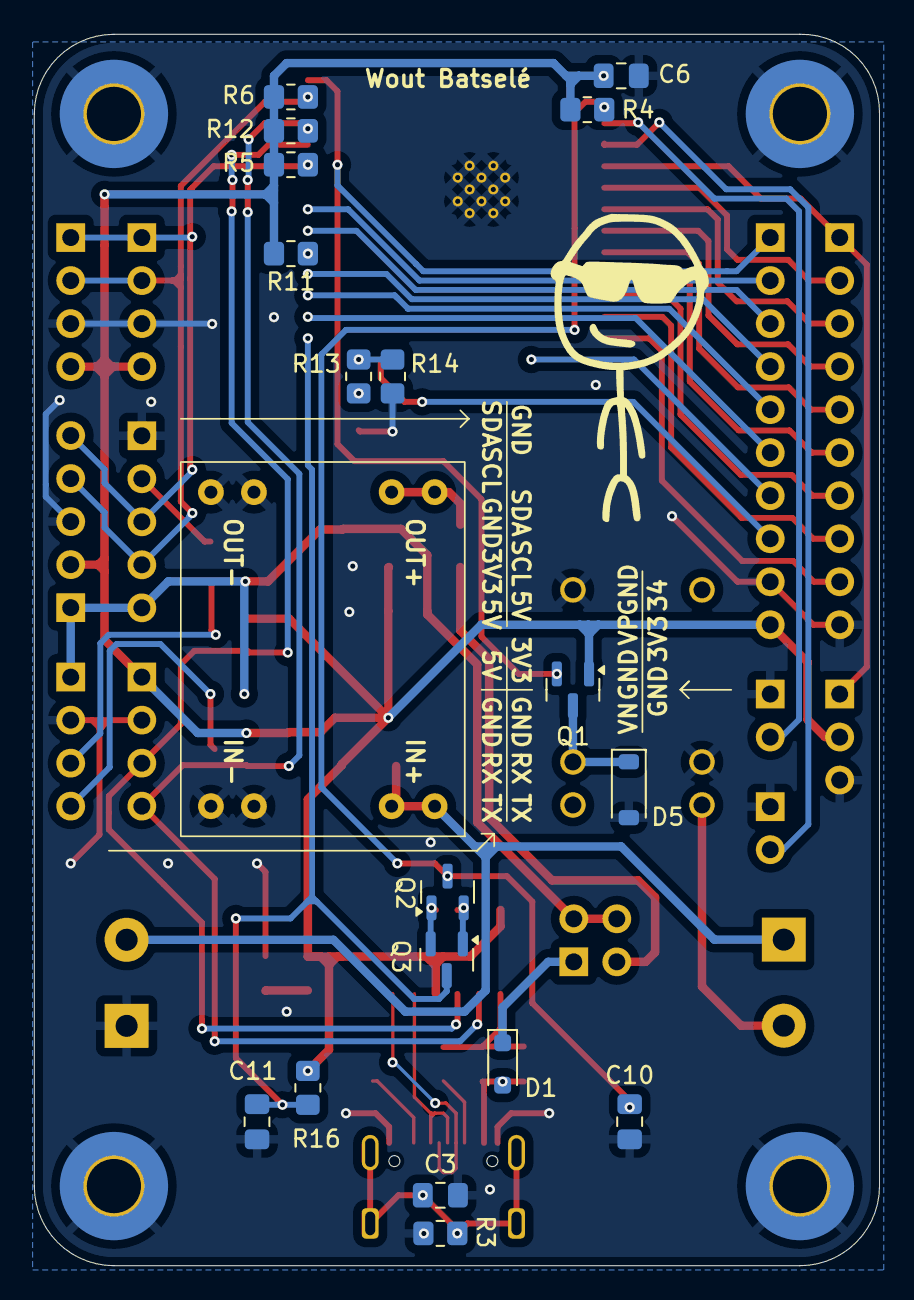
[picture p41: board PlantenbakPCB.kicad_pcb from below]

Board: 2 copper layers, 49.9 x 72.7 mm, 64 parts (18 on the bottom side), 49 nets.

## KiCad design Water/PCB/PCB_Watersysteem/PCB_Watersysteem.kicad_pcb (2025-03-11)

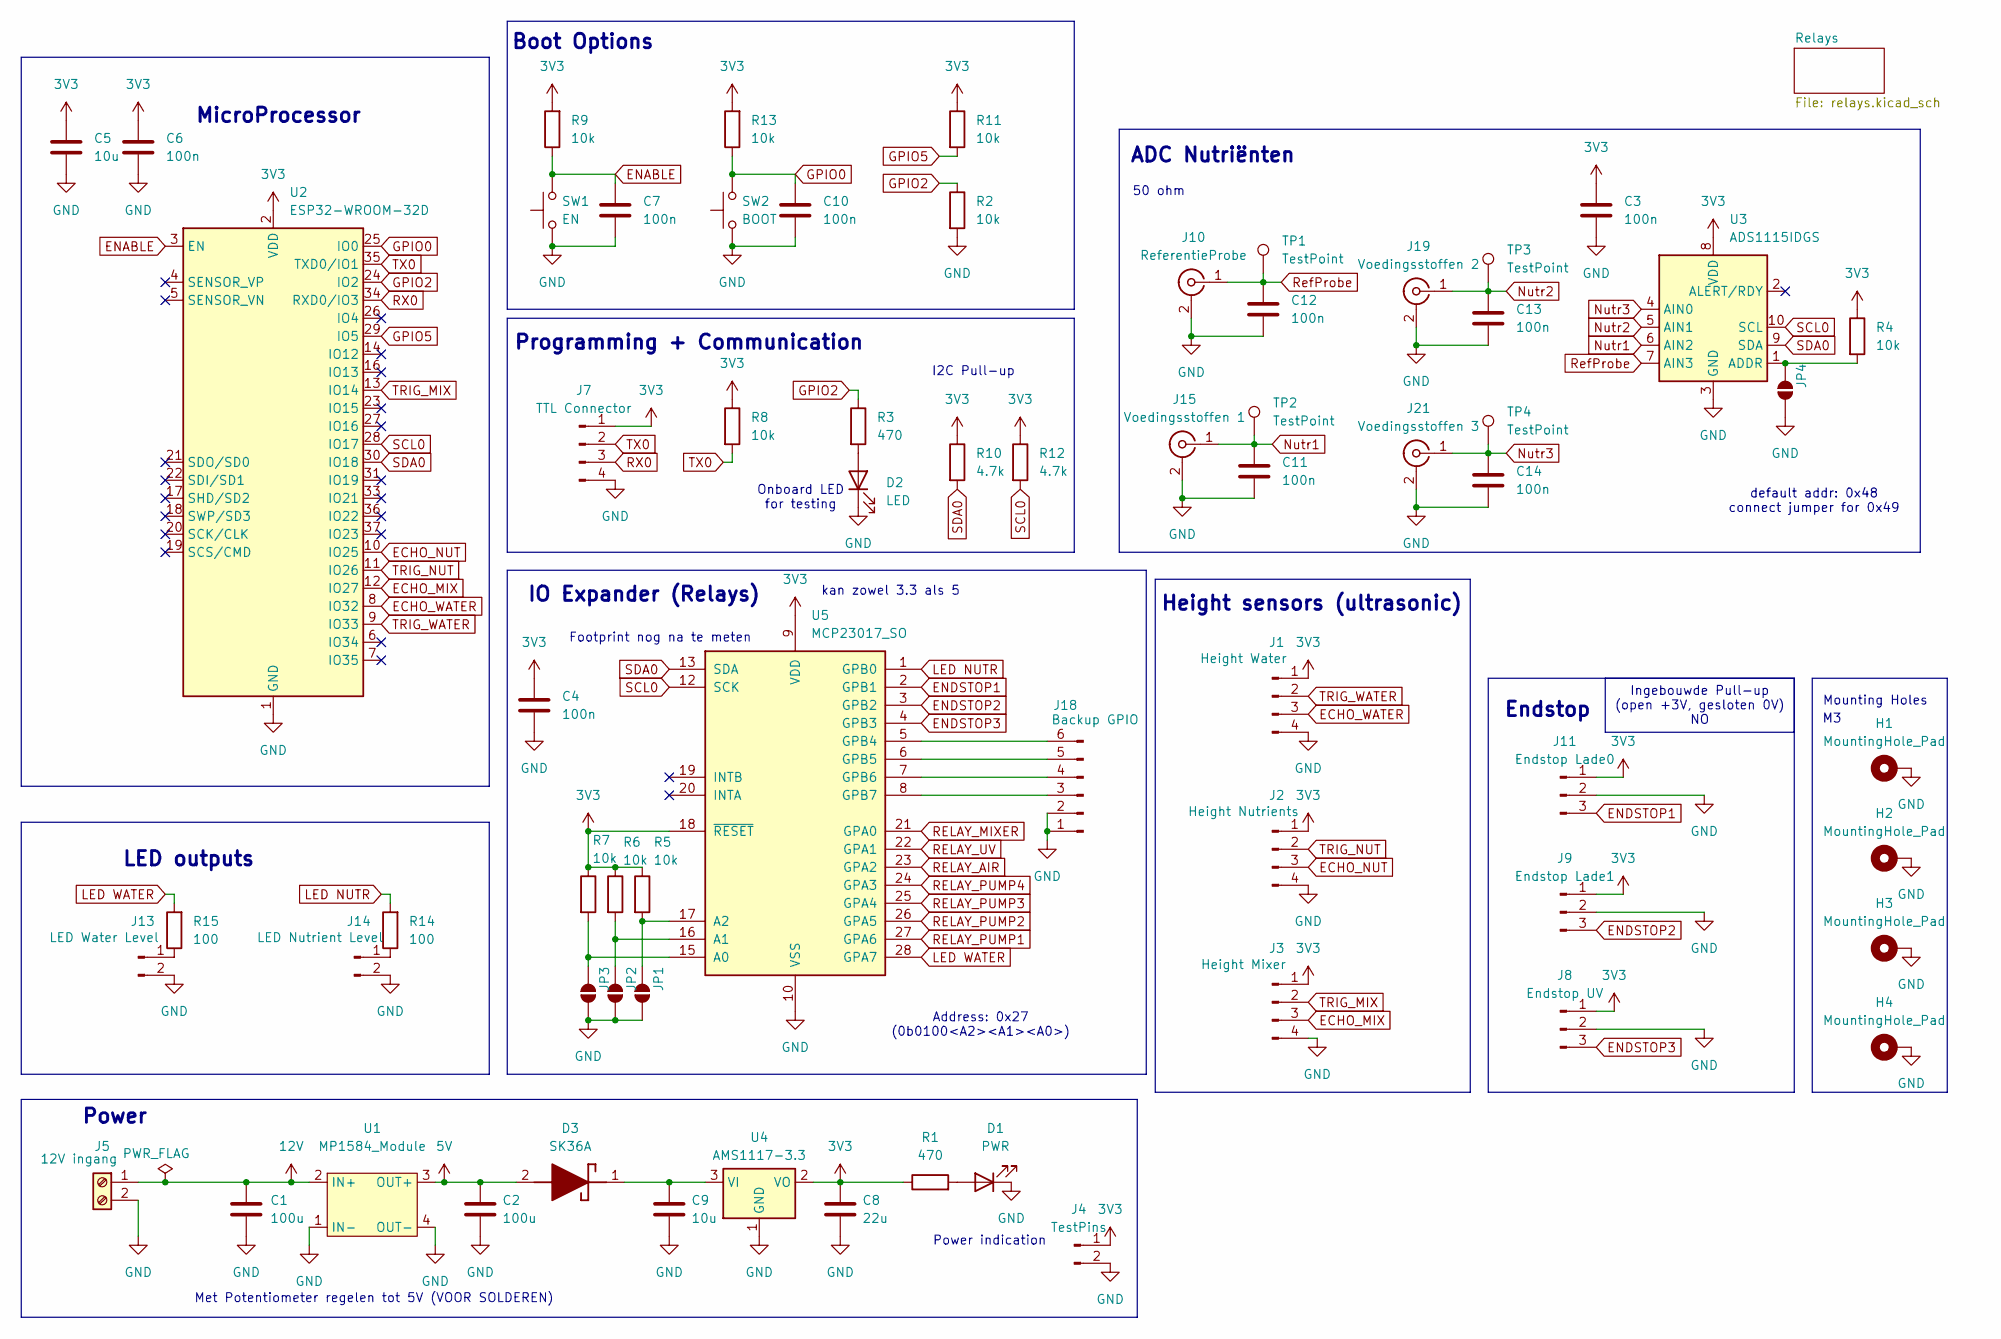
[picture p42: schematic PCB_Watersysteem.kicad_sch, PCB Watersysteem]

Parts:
C1, C2: 100u; CP_Elec_6.3x3.9
C3, C4, C6, C7, C10, C11, C12, C13, C14: 100n; C_0805_2012Metric_Pad1.18x1.45mm_HandSolder
C5, C9: 10u; C_0805_2012Metric_Pad1.18x1.45mm_HandSolder
C8: 22u; CP_EIA-3528-12_Kemet-T_Pad1.50x2.35mm_HandSolder
D1: PWR; LED_0805_2012Metric_Pad1.15x1.40mm_HandSolder
D2: LED; LED_0805_2012Metric_Pad1.15x1.40mm_HandSolder
D3: SK36A; DIOM5226X290N; Manufacturer_Part_Number SK36A; Mouser Part Number 821-SK36A
H1, H2, H3, H4: MountingHole_Pad; MountingHole_3.2mm_M3_Pad_TopBottom
J1: Height Water; PinHeader_1x04_P2.54mm_Vertical
J2: Height Nutrients; PinHeader_1x04_P2.54mm_Vertical
J3: Height Mixer; PinHeader_1x04_P2.54mm_Vertical
J4: TestPins; PinHeader_1x02_P2.54mm_Vertical
J5: 12V ingang; TerminalBlock_Phoenix_PT-1,5-2-5.0-H_1x02_P5.00mm_Horizontal
J7: TTL Connector; PinHeader_1x04_P2.54mm_Vertical
J8: Endstop UV; PinHeader_1x03_P2.54mm_Vertical
J9: Endstop Lade1; PinHeader_1x03_P2.54mm_Vertical
J10: ReferentieProbe; BNC_Amphenol_B6252HB-NPP3G-50_Horizontal
J11: Endstop Lade0; PinHeader_1x03_P2.54mm_Vertical
J13: LED Water Level; PinHeader_1x02_P2.54mm_Vertical
J14: LED Nutrient Level; PinHeader_1x02_P2.54mm_Vertical
J15: Voedingsstoffen 1; BNC_Amphenol_B6252HB-NPP3G-50_Horizontal
J18: Backup GPIO; PinHeader_1x06_P2.54mm_Vertical
J19: Voedingsstoffen 2; BNC_Amphenol_B6252HB-NPP3G-50_Horizontal
J21: Voedingsstoffen 3; BNC_Amphenol_B6252HB-NPP3G-50_Horizontal
JP1, JP2, JP3, JP4: SolderJumper_2_Open; SolderJumper-2_P1.3mm_Open_RoundedPad1.0x1.5mm
R1, R3: 470; R_0805_2012Metric_Pad1.20x1.40mm_HandSolder
R2, R4, R5, R6, R7, R8, R9, R11, R13: 10k; R_0805_2012Metric_Pad1.20x1.40mm_HandSolder
R10, R12: 4.7k; R_0805_2012Metric_Pad1.20x1.40mm_HandSolder
R14, R15: 100; R_0805_2012Metric_Pad1.20x1.40mm_HandSolder
SW1: EN; Wurth_Tactile_Switch_SPST-NO_434111043826
SW2: BOOT; Wurth_Tactile_Switch_SPST-NO_434111043826
TP1, TP2, TP3, TP4: TestPoint; TestPoint_Pad_D2.0mm
U1: MP1584_Module
U2: ESP32-WROOM-32D
U3: ADS1115IDGS; TSSOP-10_3x3mm_P0.5mm
U4: AMS1117-3.3; SOT-223-3_TabPin2
U5: MCP23017_SO; SOIC-28W_7.5x17.9mm_P1.27mm

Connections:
3V3: C3.1, C4.1, C5.1, C6.1, C8.1, J1.1, J2.1, J3.1, J4.1, J7.1, J8.1, J9.1, J11.1, R1.1, R4.1, R5.1, R6.1, R7.1, R8.1, R9.2, R10.1, R11.1, R12.1, R13.2, U2.2 (VDD), U3.8 (VDD), U4.2 (VO), U5.9 (VDD), U5.18 (~RESET)
5V: C2.1, D3.2 (A), U1.3 (OUT+); also elsewhere on the board
12V: C1.1, J5.1, U1.2 (IN+); also elsewhere on the board
ECHO_MIX: J3.3, U2.12 (IO27)
ECHO_NUT: J2.3, U2.10 (IO25)
ECHO_WATER: J1.3, U2.8 (IO32)
ENABLE: C7.1, R9.1, SW1.1, U2.3 (EN)
ENDSTOP1: J11.3, U5.2 (GPB1)
ENDSTOP2: J9.3, U5.3 (GPB2)
ENDSTOP3: J8.3, U5.4 (GPB3)
GND: C1.2, C2.2, C3.2, C4.2, C5.2, C6.2, C7.2, C8.2, C9.2, C10.2, C11.2, C12.2, C13.2, C14.2, D1.1 (K), D2.1 (K), H1.1, H2.1, H3.1, H4.1, J1.4, J2.4, J3.4, J4.2, J5.2, J7.4, J8.2, J9.2, J10.2 (Ext), J11.2, J13.2, J14.2, J15.2 (Ext), J18.1, J18.2, J19.2 (Ext), J21.2 (Ext), JP1.1 (A), JP2.1 (A), JP3.1 (A), JP4.1 (A), R2.2, SW1.2, SW2.2, U1.1 (IN-), U1.4 (OUT-), U2.1 (GND), U2.15 (GND), U2.38 (GND), U2.39 (GND), U3.3 (GND), U4.1 (GND), U5.10 (VSS); also elsewhere on the board
GPIO0: C10.1, R13.1, SW2.1, U2.25 (IO0)
GPIO2: R2.1, R3.1, U2.24 (IO2)
GPIO5: R11.2, U2.29 (IO5)
LED NUTR: R14.2, U5.1 (GPB0)
LED WATER: R15.2, U5.28 (GPA7)
unnamed: D1.2 (A), R1.2
unnamed: D2.2 (A), R3.2
unnamed: C9.1, D3.1 (K), U4.3 (VI)
unnamed: J13.1, R15.1
unnamed: J14.1, R14.1
unnamed: J18.3, U5.8 (GPB7)
unnamed: J18.4, U5.7 (GPB6)
unnamed: J18.5, U5.6 (GPB5)
unnamed: J18.6, U5.5 (GPB4)
unnamed: JP1.2 (B), R5.2, U5.17 (A2)
unnamed: JP2.2 (B), R6.2, U5.16 (A1)
unnamed: JP3.2 (B), R7.2, U5.15 (A0)
unnamed: JP4.2 (B), R4.2, U3.1 (ADDR)
Nutr1: C11.1, J15.1 (In), TP2.1, U3.6 (AIN2)
Nutr2: C13.1, J19.1 (In), TP3.1, U3.5 (AIN1)
Nutr3: C14.1, J21.1 (In), TP4.1, U3.4 (AIN0)
RELAY_AIR: U5.23 (GPA2); also elsewhere on the board
RELAY_MIXER: U5.21 (GPA0); also elsewhere on the board
RELAY_PUMP1: U5.27 (GPA6); also elsewhere on the board
RELAY_PUMP2: U5.26 (GPA5); also elsewhere on the board
RELAY_PUMP3: U5.25 (GPA4); also elsewhere on the board
RELAY_PUMP4: U5.24 (GPA3); also elsewhere on the board
RELAY_UV: U5.22 (GPA1); also elsewhere on the board
RX0: J7.3, U2.34 (RXD0/IO3)
RefProbe: C12.1, J10.1 (In), TP1.1, U3.7 (AIN3)
SCL0: R12.2, U2.28 (IO17), U3.10 (SCL), U5.12 (SCK)
SDA0: R10.2, U2.30 (IO18), U3.9 (SDA), U5.13 (SDA)
TRIG_MIX: J3.2, U2.13 (IO14)
TRIG_NUT: J2.2, U2.11 (IO26)
TRIG_WATER: J1.2, U2.9 (IO33)
TX0: J7.2, R8.2, U2.35 (TXD0/IO1)

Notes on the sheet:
Endstop
kan zowel 3.3 als 5
Height sensors (ultrasonic)
Address: 0x27 (0b0100<A2><A1><A0>)
Mounting Holes
I2C Pull-up
default addr: 0x48 connect jumper for 0x49
Boot Options
ADC Nutriënten
MicroProcessor
50 ohm
IO Expander (Relays)
Footprint nog na te meten
Onboard LED for testing
LED outputs
Power indication
Programming + Communication
Met Potentiometer regelen tot 5V (VOOR SOLDEREN)
Power
Ingebouwde Pull-up (open +3V, gesloten 0V) NO

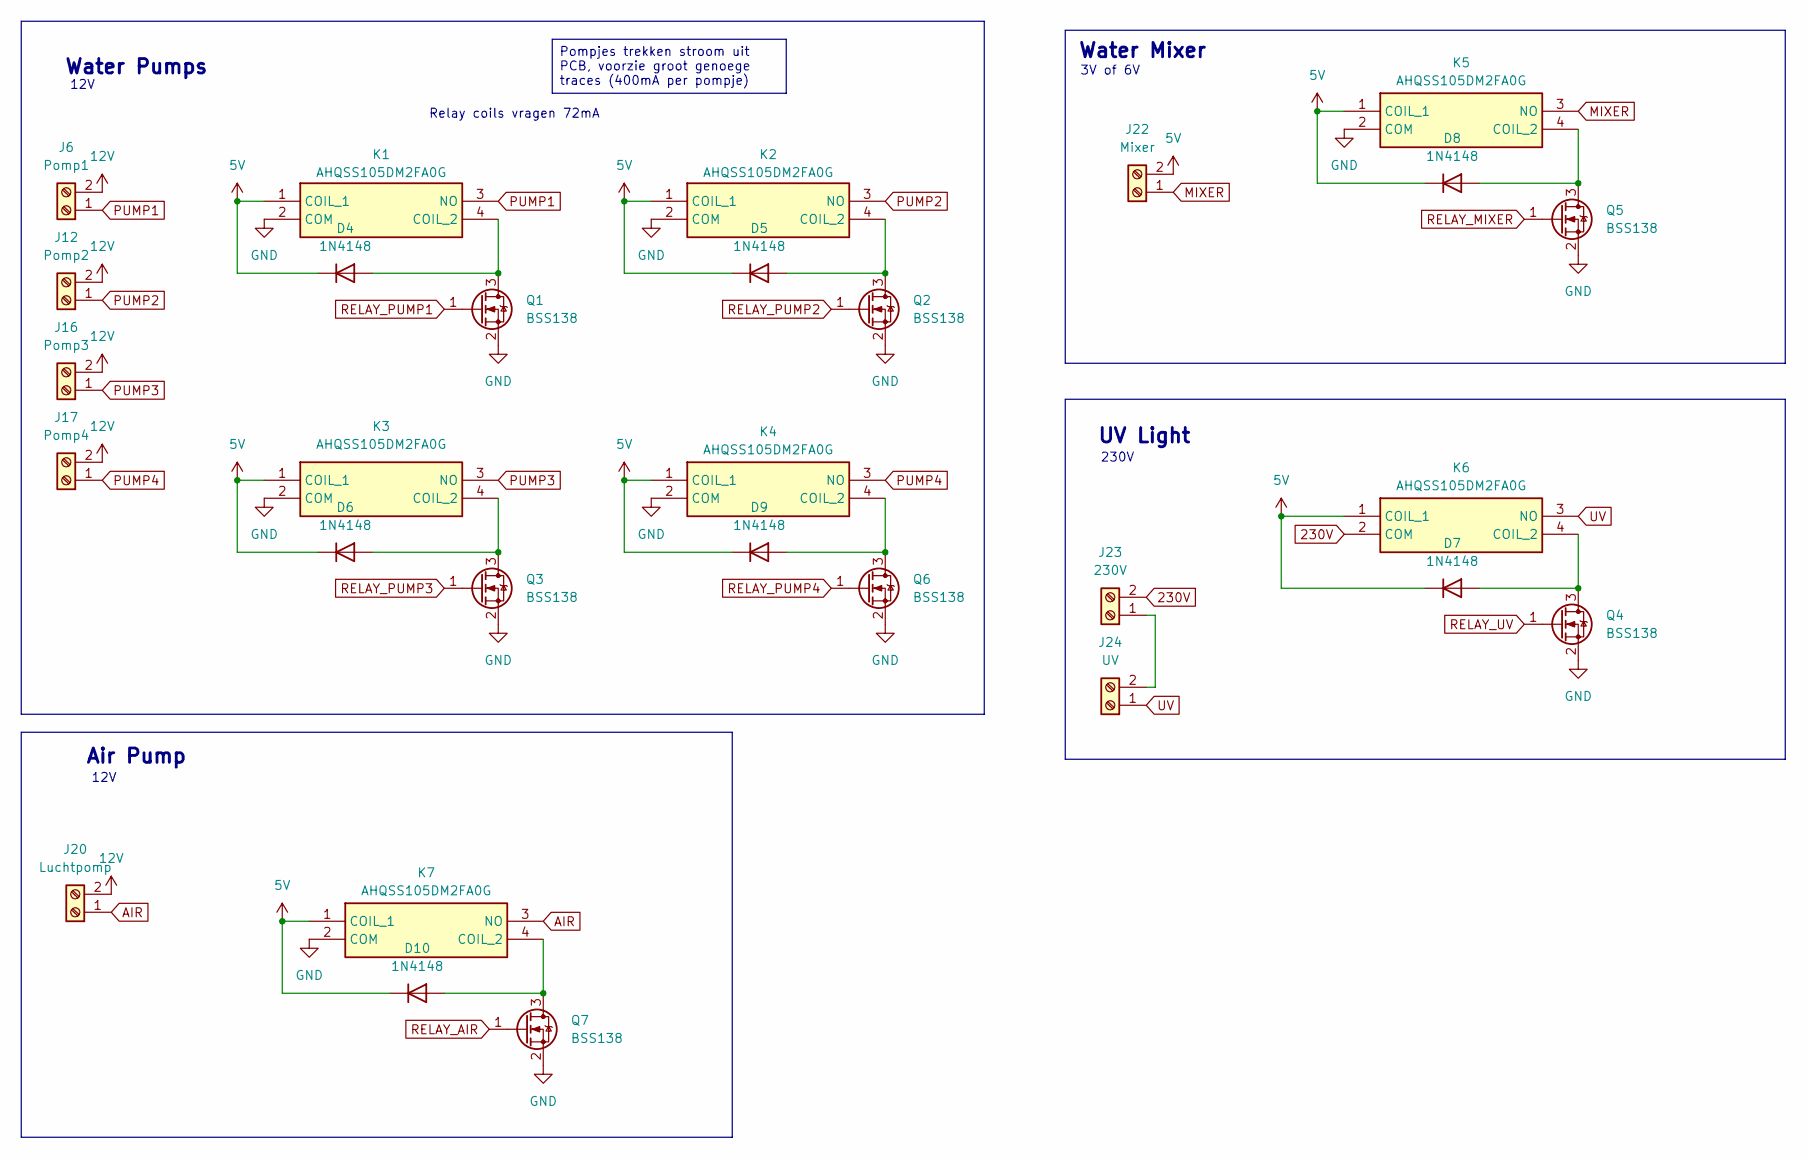
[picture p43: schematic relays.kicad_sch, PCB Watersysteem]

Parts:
D4, D5, D6, D7, D8, D9, D10: 1N4148; D_0805_2012Metric_Pad1.15x1.40mm_HandSolder
J6: Pomp1; TerminalBlock_Phoenix_PT-1,5-2-5.0-H_1x02_P5.00mm_Horizontal
J12: Pomp2; TerminalBlock_Phoenix_PT-1,5-2-5.0-H_1x02_P5.00mm_Horizontal
J16: Pomp3; TerminalBlock_Phoenix_PT-1,5-2-5.0-H_1x02_P5.00mm_Horizontal
J17: Pomp4; TerminalBlock_Phoenix_PT-1,5-2-5.0-H_1x02_P5.00mm_Horizontal
J20: Luchtpomp; TerminalBlock_Phoenix_PT-1,5-2-5.0-H_1x02_P5.00mm_Horizontal
J22: Mixer; TerminalBlock_Phoenix_PT-1,5-2-5.0-H_1x02_P5.00mm_Horizontal
J23: 230V; TerminalBlock_Phoenix_PT-1,5-2-5.0-H_1x02_P5.00mm_Horizontal
J24: UV; TerminalBlock_Phoenix_PT-1,5-2-5.0-H_1x02_P5.00mm_Horizontal
K1, K2, K3, K4, K5, K6, K7: AHQSS105DM2FA0G; Manufacturer_Part_Number AHQSS105DM2FA0G; Mouser Part Number 523-AHQSS105DM2FA0G
Q1, Q2, Q3, Q4, Q5, Q6, Q7: BSS138; SOT-23

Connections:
5V: D4.1 (K), D5.1 (K), D6.1 (K), D7.1 (K), D8.1 (K), D9.1 (K), D10.1 (K), J22.2, K1.1 (COIL_1), K2.1 (COIL_1), K3.1 (COIL_1), K4.1 (COIL_1), K5.1 (COIL_1), K6.1 (COIL_1), K7.1 (COIL_1); also elsewhere on the board
12V: J6.2, J12.2, J16.2, J17.2, J20.2; also elsewhere on the board
230V: J23.2, K6.2 (COM)
AIR: J20.1, K7.3 (NO)
GND: K1.2 (COM), K2.2 (COM), K3.2 (COM), K4.2 (COM), K5.2 (COM), K7.2 (COM), Q1.2 (S), Q2.2 (S), Q3.2 (S), Q4.2 (S), Q5.2 (S), Q6.2 (S), Q7.2 (S); also elsewhere on the board
MIXER: J22.1, K5.3 (NO)
unnamed: D4.2 (A), K1.4 (COIL_2), Q1.3 (D)
unnamed: D5.2 (A), K2.4 (COIL_2), Q2.3 (D)
unnamed: D6.2 (A), K3.4 (COIL_2), Q3.3 (D)
unnamed: D7.2 (A), K6.4 (COIL_2), Q4.3 (D)
unnamed: D8.2 (A), K5.4 (COIL_2), Q5.3 (D)
unnamed: D9.2 (A), K4.4 (COIL_2), Q6.3 (D)
unnamed: D10.2 (A), K7.4 (COIL_2), Q7.3 (D)
unnamed: J23.1, J24.2
PUMP1: J6.1, K1.3 (NO)
PUMP2: J12.1, K2.3 (NO)
PUMP3: J16.1, K3.3 (NO)
PUMP4: J17.1, K4.3 (NO)
RELAY_AIR: Q7.1 (G); also elsewhere on the board
RELAY_MIXER: Q5.1 (G); also elsewhere on the board
RELAY_PUMP1: Q1.1 (G); also elsewhere on the board
RELAY_PUMP2: Q2.1 (G); also elsewhere on the board
RELAY_PUMP3: Q3.1 (G); also elsewhere on the board
RELAY_PUMP4: Q6.1 (G); also elsewhere on the board
RELAY_UV: Q4.1 (G); also elsewhere on the board
UV: J24.1, K6.3 (NO)

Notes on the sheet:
12V
3V of 6V
UV Light
230V
Water Mixer
Air Pump
Water Pumps
Relay coils vragen 72mA
Pompjes trekken stroom uit PCB, voorzie groot genoege traces (400mA per pompje)

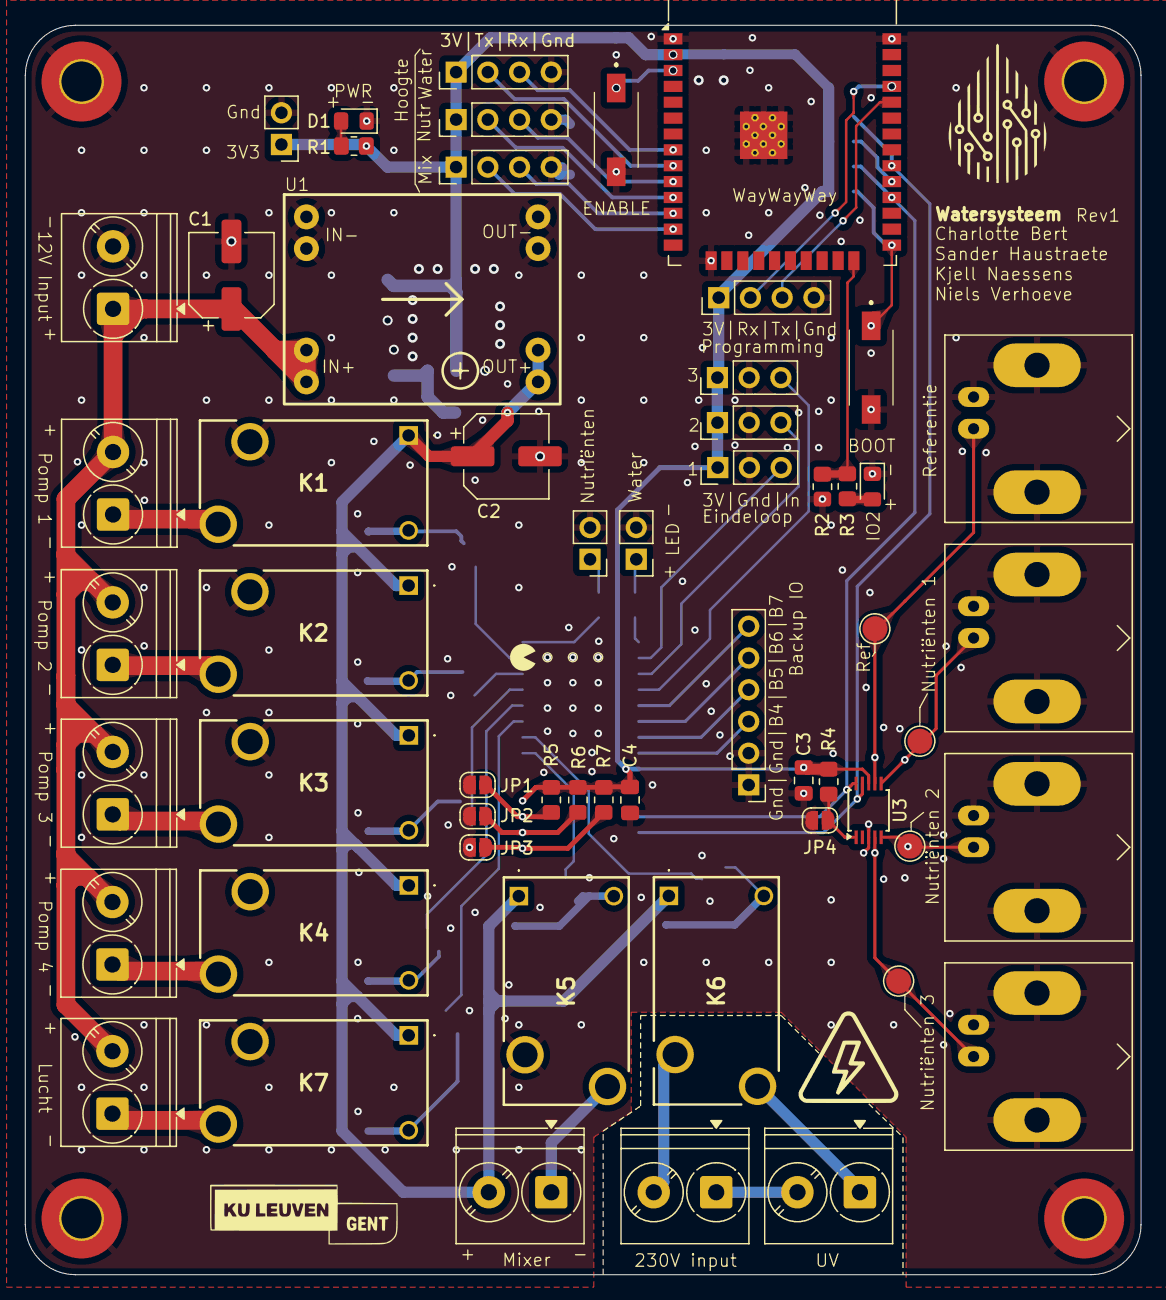
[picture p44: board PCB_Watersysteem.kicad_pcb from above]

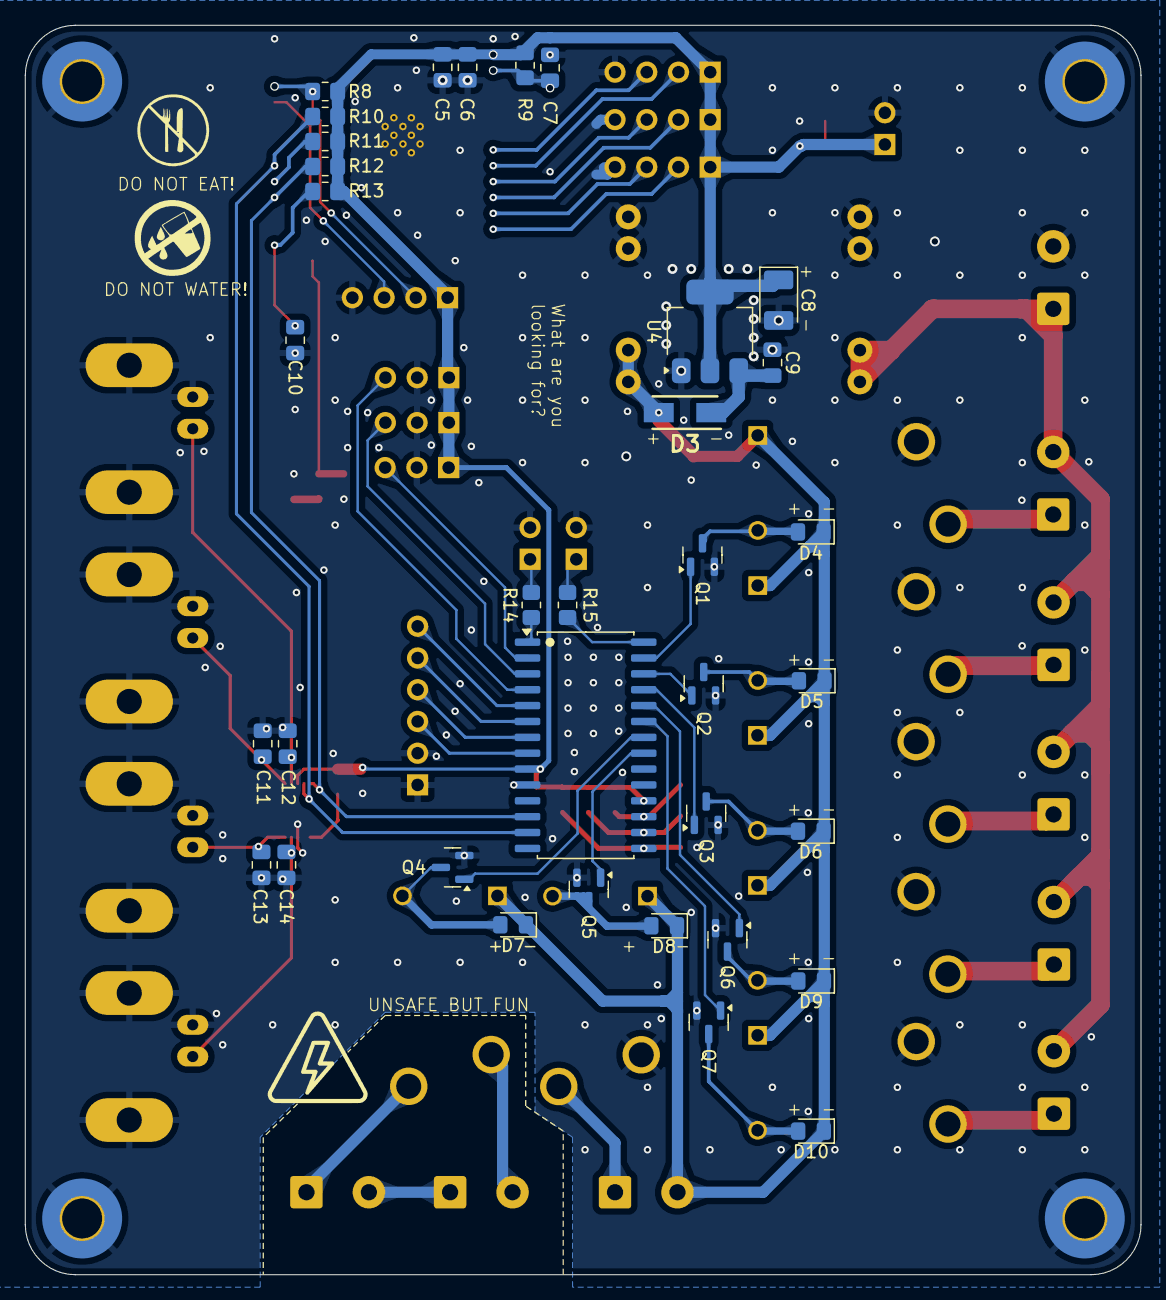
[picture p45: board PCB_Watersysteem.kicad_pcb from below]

Board: 2 copper layers, 89.3 x 100.0 mm, 96 parts (35 on the bottom side), 63 nets.

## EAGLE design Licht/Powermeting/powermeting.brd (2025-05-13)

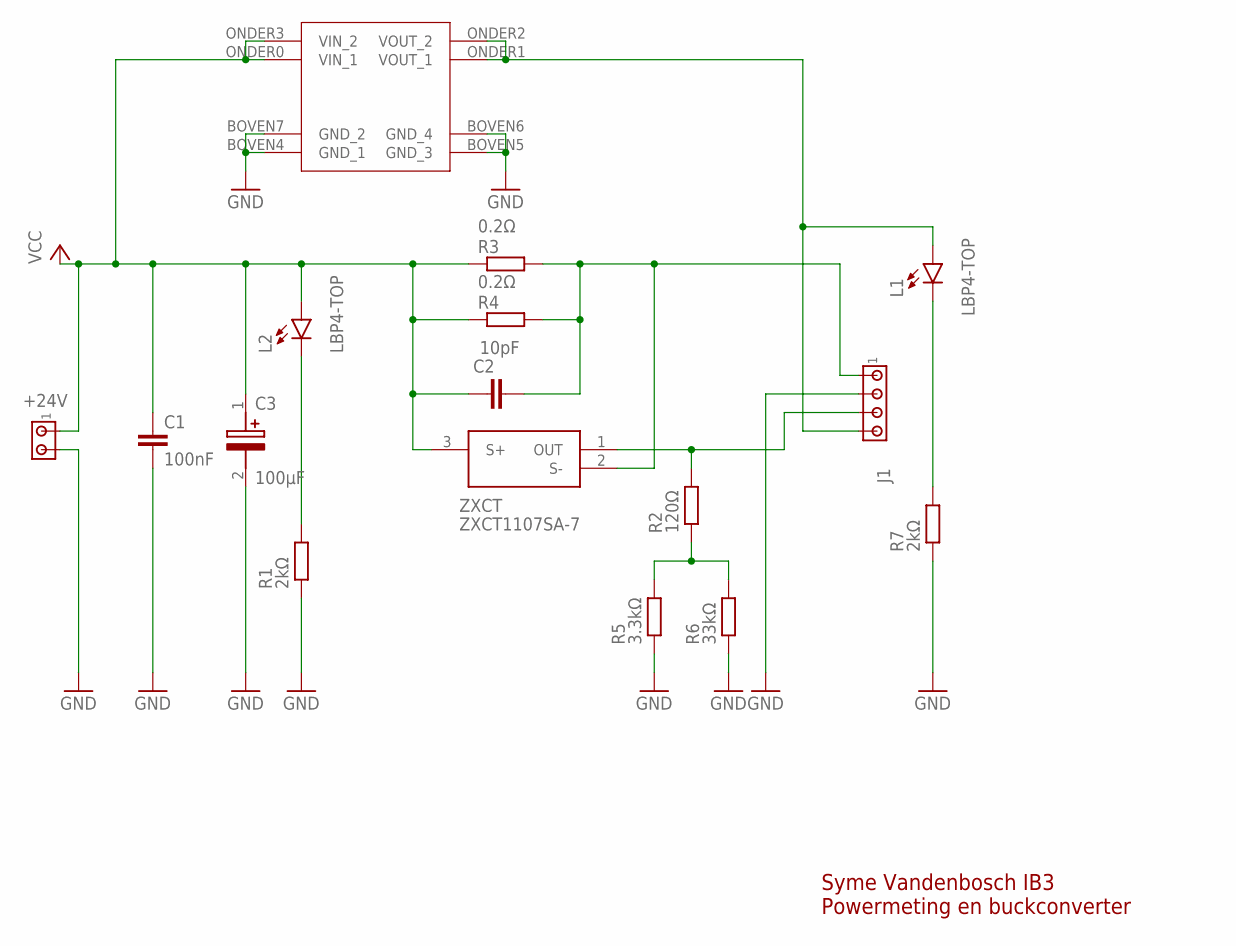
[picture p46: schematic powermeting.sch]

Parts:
+24V: MTA02-100; 10X02MTA
C1: 100nF; C0805K
C2: 10pF; C0805K
C3: 100µF; EEHZA1H100R
J1: MTA04-100; 10X04MTA
L1, L2: LBP4-TOP; LED3MM
R1, R7: 2kΩ; M0805
R2: 120Ω; M0805
R3, R4: 0.2Ω; M1206
R5: 3.3kΩ; M0805
R6: 33kΩ; M0805
U$1: BUCK
ZXCT: ZXCT1107SA-7; SOT96P240X110-3N

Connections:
GND: +24V.2, C1.2, C3.2 (-), J1.2, R1.1, R5.1, R6.1, R7.1, U$1.BOVEN4 (GND_1), U$1.BOVEN5 (GND_3), U$1.BOVEN6 (GND_4), U$1.BOVEN7 (GND_2)
unnamed: L1.K (C), R7.2
unnamed: L2.K (C), R1.2
unnamed: R2.1, R5.2, R6.2
unnamed: C2.2, J1.1, R3.1, R4.1, ZXCT.2 (S-)
unnamed: J1.4, L1.A, U$1.ONDER1 (VOUT_1), U$1.ONDER2 (VOUT_2)
unnamed: J1.3, R2.2, ZXCT.1 (OUT)
VCC: +24V.1, C1.1, C2.1, C3.1 (+), L2.A, R3.2, R4.2, U$1.ONDER0 (VIN_1), U$1.ONDER3 (VIN_2), ZXCT.3 (S+)

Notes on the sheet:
Syme Vandenbosch IB3 Powermeting en buckconverter

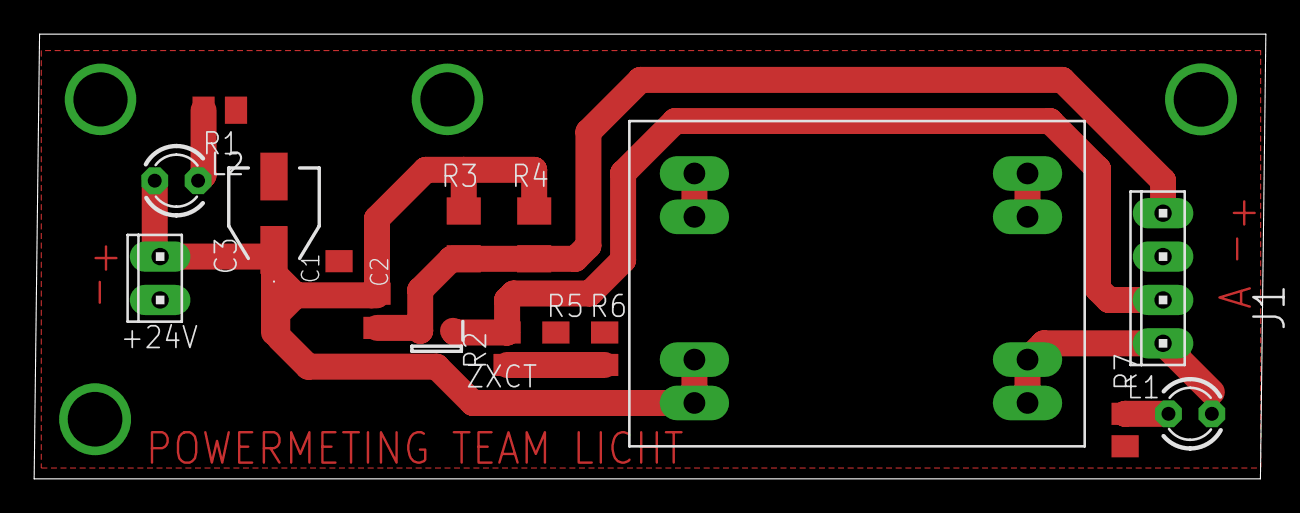
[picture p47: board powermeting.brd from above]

Board: 2 copper layers, 72.1 x 26.0 mm, 16 parts (0 on the bottom side), 8 nets.

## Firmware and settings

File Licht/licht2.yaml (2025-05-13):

esphome:
  name: licht-lade-2
  friendly_name: licht lade 2
  on_boot:
    priority: 600  # Runs after hardware initialization
    then:
      - script.execute: all_off
      #show the states of the ledpg and fault pins
      - text_sensor.template.publish:
          id: ledpg_1_state
          state: !lambda 'return id(ledpg_1).state ? "HIGH" : "LOW";'
      - text_sensor.template.publish:
          id: fault_1_state
          state: !lambda 'return id(fault_1).state ? "HIGH" : "LOW";'
      - text_sensor.template.publish:
          id: ledpg_2_state
          state: !lambda 'return id(ledpg_2).state ? "HIGH" : "LOW";'
      - text_sensor.template.publish:
          id: fault_2_state
          state: !lambda 'return id(fault_2).state ? "HIGH" : "LOW";'
      - script.execute: start_routine
      - script.wait: start_routine
      - script.execute: eco
   
#       when using driver 3 => uncomment this, enable and the individual pwm controlls (in script)
#      - text_sensor.template.publish:
#          id: ledpg_3_state
#          state: !lambda 'return id(ledpg_3).state ? "HIGH" : "LOW";'
#      - text_sensor.template.publish:
#          id: fault_3_state
#          state: !lambda 'return id(fault_3).state ? "HIGH" : "LOW";'

esp32:
  board: esp32dev
  framework:
    type: arduino

# Enable logging
logger:

# Enable Home Assistant API
api:
  encryption:
    key: 
  reboot_timeout: 0s
  on_client_disconnected:
    then: 
      script.execute: handle_fault_or_ledpg_low

ota:
  - platform: esphome
    password: 

wifi:
  ssid: !secret wifi_ssid
  password: !secret wifi_password

  # Enable fallback hotspot (captive portal) in case wifi connection fails
  ap:
    ssid: "Licht2 Fallback Hotspot"
    password: "Lumos_Maxima"
    manual_ip:
      static_ip: 192.168.0.1
      gateway: 192.168.0.1
      subnet: 255.255.255.0
captive_portal:

# Enable basic web server
web_server:
  port: 80
  version: 3

time:
  - platform: homeassistant
    id: homeassistant_time

output:
#driver 1
  - platform: ledc
    id: pwm_output_1_blauw
    pin: 5
    frequency: 1000 Hz #down to 0.%
  - platform: ledc
    id: pwm_output_1_rood
    pin: 18
    frequency: 1000 Hz
  - platform: ledc
    id: pwm_output_1_ver_rood
    pin: 19
    frequency: 1000 Hz
#driver 2
  - platform: ledc
    id: pwm_output_2_blauw
    pin: 12
    frequency: 1000 Hz #down to 0.%
  - platform: ledc
    id: pwm_output_2_rood
    pin: 13
    frequency: 1000 Hz
  - platform: ledc
    id: pwm_output_2_ver_rood
    pin: 15
    frequency: 1000 Hz
#driver 3
  - platform: ledc
    id: pwm_output_3_blauw
    pin: 32
    frequency: 1000 Hz #down to 0.%
  - platform: ledc
    id: pwm_output_3_rood
    pin: 33
    frequency: 1000 Hz
  - platform: ledc
    id: pwm_output_3_ver_rood
    pin: 25
    frequency: 1000 Hz

globals:
  - id: pwm_level_1_blauw
    type: float
    restore_value: no
    initial_value: '0.0'
  - id: pwm_level_1_rood
    type: float
    restore_value: no
    initial_value: '0.0'
  - id: pwm_level_1_ver_rood
    type: float
    restore_value: no
    initial_value: '0.0'
  - id: pwm_level_2_blauw
    type: float
    restore_value: no
    initial_value: '0.0'
  - id: pwm_level_2_rood
    type: float
    restore_value: no
    initial_value: '0.0'
  - id: pwm_level_2_ver_rood
    type: float
    restore_value: no
    initial_value: '0.0'
  - id: pwm_level_3_blauw
    type: float
    restore_value: no
    initial_value: '0.0'
  - id: pwm_level_3_rood
    type: float
    restore_value: no
    initial_value: '0.0'
  - id: pwm_level_3_ver_rood
    type: float
    restore_value: no
    initial_value: '0.0'

  - id: pwm_kleur_global_blauw
    type: float
    restore_value: no
    initial_value: '0.0'
  - id: pwm_kleur_global_rood
    type: float
    restore_value: no
    initial_value: '0.0'
  - id: pwm_kleur_global_ver_rood
    type: float
    restore_value: no
    initial_value: '0.0'

    # Backups voor PWM-niveaus bij foutdetectie
  - id: pwm_level_backup_1_blauw
    type: float
    restore_value: no
    initial_value: '0.0'
  - id: pwm_level_backup_1_rood
    type: float
    restore_value: no
    initial_value: '0.0'
  - id: pwm_level_backup_1_ver_rood
    type: float
    restore_value: no
    initial_value: '0.0'

  - id: pwm_level_backup_2_blauw
    type: float
    restore_value: no
    initial_value: '0.0'
  - id: pwm_level_backup_2_rood
    type: float
    restore_value: no
    initial_value: '0.0'
  - id: pwm_level_backup_2_ver_rood
    type: float
    restore_value: no
    initial_value: '0.0'

  - id: pwm_level_backup_3_blauw
    type: float
    restore_value: no
    initial_value: '0.0'
  - id: pwm_level_backup_3_rood
    type: float
    restore_value: no
    initial_value: '0.0'
  - id: pwm_level_backup_3_ver_rood
    type: float
    restore_value: no
    initial_value: '0.0'
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

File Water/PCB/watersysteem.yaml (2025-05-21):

### The Ultimate Water System
# written by Kjell

esphome:
  name: watersysteem
  friendly_name: Watersysteem

esp32:
  board: esp32dev
  framework:
    type: arduino

# Enable logging
logger:

# Enable Home Assistant API
api:
  encryption:
    key: "BoEliEKdwduVeAiNUockde0/TeNXvJCees77YDFz7jA="

ota:
  - platform: esphome
    password: "c50539ee1af9e506b6007999eb8f6d14"

wifi:
  ssid: !secret wifi_ssid
  password: !secret wifi_password

  # Enable fallback hotspot (captive portal) in case wifi connection fails
  ap:
    ssid: "Watersysteem Fallback Hotspot"
    password: "V2dJKfdCVYAC"

captive_portal:
    
# Enable basic web server for easy debugging
#web_server:
#  port: 80
#  version: 3

# haal tijd op van de server
time:
  - platform: homeassistant
    id: homeassistant_time

# status LED
status_led:
  pin: GPIO2

# Setup I2C for communication
i2c:
  sda: GPIO18
  scl: GPIO17
  scan: True

### IO EXPANDER ###
mcp23017:
  - id: 'expander'
    address: 0x27

### ADC ###
ads1115:
  - address: 0x49

# OUTPUTS
switch:
  # ONBOARD LED
  #- platform: gpio
  #  name: "Onboard LED"
  #  pin: GPIO2
  # WATER LED
  - platform: gpio
    name: "Status LED Rood"
    inverted: True
    pin:
      mcp23xxx: expander
      number: 7 #A7
      mode:
        output: True
  # NUTRIENTS LED
  - platform: gpio
    name: "Status LED Groen"
    inverted: True
    pin:
      mcp23xxx: expander
      number: 8 #B0
      mode:
        output: True
  # RELAYS
  - platform: gpio
    name: "Mixer"
    id: mixer
    pin:
      mcp23xxx: expander
      number: 0 #A0
      mode:
        output: True
  - platform: gpio
    name: "UV lamp"
    id: uv_lamp
    pin:
      mcp23xxx: expander
      number: 1 #A1
      mode:
        output: True
  - platform: gpio
    name: "Luchtpomp"
    pin:
      mcp23xxx: expander
      number: 2 #A2
      mode:
        output: True
  - platform: gpio
    name: "Pomp water"
    pin:
      mcp23xxx: expander
      number: 6 #A6
      mode:
        output: True
  - platform: gpio
    name: "Pomp voedingsstoffen"
    pin:
      mcp23xxx: expander
      number: 5 #A5
      mode:
        output: True
  - platform: gpio
    name: "Pomp lade voorkant"
    pin:
      mcp23xxx: expander
      number: 4 #A4
      mode:
        output: True
  - platform: gpio
    name: "Pomp lade achterkant"
    pin:
      mcp23xxx: expander
      number: 3 #A3
      mode:
        output: True

# INPUTS
sensor:
  # HEIGHT SENSORS (ULTRASONIC)
  - platform: ultrasonic
    name: "Hoogte Nutriënten"
    trigger_pin: GPIO26
    echo_pin: GPIO25
    update_interval: 1s
    filters:
    - filter_out: nan  # Filter out any invalid readings
    - median:
        window_size: 5
        send_every: 1
        send_first_at: 1
    - lambda: |- # 0.04 = 100%, 0.145 = 0%
        return (x - 0.145) * (100.0 - 0.0) / (0.04 - 0.145) + 0.0;
    unit_of_measurement: "%"

  - platform: ultrasonic
    name: "Hoogte Water"
    trigger_pin: GPIO33
    echo_pin: GPIO32
    update_interval: 1s
    filters:
    - filter_out: nan  # Filter out any invalid readings
    - median:
        window_size: 5
        send_every: 1
        send_first_at: 1
    - lambda: |- # 0.04 = 100%, 0.14 = 0%
        return (x - 0.145) * (100.0 - 0.0) / (0.04 - 0.145) + 0.0;
    unit_of_measurement: "%"
  - platform: ultrasonic
    name: "Hoogte mixer"
    trigger_pin: GPIO14
    echo_pin: GPIO27
    update_interval: 1s
    filters:
    - filter_out: nan  # Filter out any invalid readings
    - median:
        window_size: 5
        send_every: 1
        send_first_at: 1
    - lambda: |- # 0.04 = 100%, 0.13 = 0%
        return (x - 0.13) * 100.0 / (0.04 - 0.13);
    unit_of_measurement: "%"
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

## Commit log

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2025-01-27 Added 3D-models
    Added 3D-models and assemblies of the water system and common connector (both still WIP)
    [Common_Connector.SLDASM, Common_Connector_F_Plate.SLDPRT, Common_Connector_M_Plate.SLDPRT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]
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2025-02-18 Update 3D modellen
    Plantenbakken herwerkt (randen weggevijld zodat ze onderaan passen) + Buitenste 'shell' van kast
    [Ineengestoken_Kast.SLDASM, Kast.SLDPRT, Waterbak.SLDPRT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]
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2025-02-18 Add files via upload
    Gantt Chart
    [Online Gantt 20250218.csv]
2025-02-19 PCB Watersysteem initial commit
    Ontwerp PCB initial commit: deel van schema van PCB, custom symbol + footprints (MP1584 buck converter module), symbol+footprint van 5V relais
    [PCB_Watersysteem.kicad_pcb, PCB_Watersysteem.kicad_sch]
2025-02-23 Update PCB watersysteem
    [PCB_Watersysteem.kicad_sch]
2025-02-24 PCB update
    ADC verbonden, LED outputs, Eindeloops, Voorbeeld relais
    [PCB_Watersysteem.kicad_sch, relays.kicad_sch]
2025-02-25 Add files via upload
    Vergeten file
    [Gantt Chart.xlsx]
2025-02-25 update progress team plantenbak
    [Gantt Chart.xlsx]
2025-02-25 Update PCB
    Extra terminals
    [PCB_Watersysteem.kicad_sch, relays.kicad_sch]
2025-02-25 Update PCB
    relaisschakelingen verder afgewerkt, endstops afgewerkt, bezig met ultrasone sensors
    [PCB_Watersysteem.kicad_sch, relays.kicad_sch]
2025-02-25 Update PCB
    deel footprints geselecteerd, hoogtesensoren ingesteld
    [PCB_Watersysteem.kicad_sch, relays.kicad_sch]
2025-02-26 Update PCB
    Footprints LEDs toegevoegd
    [PCB_Watersysteem.kicad_sch]
2025-02-26 Update PCB
    16 bit I2C IO expander toegevoegd (juiste footprint nog na te meten)
    [PCB_Watersysteem.kicad_sch]
2025-02-26 Update PCB
    16 bit IO-expander ingesteld
    [PCB_Watersysteem.kicad_sch]
2025-02-26 PCB update
    Testpunten, relaisschakelingen afgewerkt, adres io expander wijzigbaar, enkele footprints
    [PCB_Watersysteem.kicad_sch, relays.kicad_sch]
2025-02-26 Update PCB
    Switch library toegevoegd, IO expander ontkoppel toegevoegd
    [PCB_Watersysteem.kicad_sch]
2025-02-27 Update PCB
    transistoren vervangen door mosfets
    [relays.kicad_sch]
2025-02-27 Update PCB
    Footprints toegevoegd
    [PCB_Watersysteem.kicad_sch]
2025-03-01 Update PCB
    IO gemapt, Condensator ADC, Schematic geprint
    [PCB_Watersysteem.kicad_sch, relays.kicad_sch]
2025-03-03 Update PCB
    BNC Connectoren ingevoegd, extra footprints
    [PCB_Watersysteem.kicad_sch]
2025-03-04 Update PCB
    alle footprints staan correct, alles in PCB geïmporteert
    [PCB_Watersysteem.kicad_pcb, PCB_Watersysteem.kicad_sch, relays.kicad_sch]
2025-03-04 componenten gegroepeerd
    [PCB_Watersysteem.kicad_pcb]
2025-03-04 Indeling gemaakt
    [PCB_Watersysteem.kicad_pcb]
2025-03-05 Update PCB
    Placing en routing van vermogen, grootste componenten
    [PCB_Watersysteem.kicad_pcb, PCB_Watersysteem.kicad_sch]
2025-03-05 Update PCB
    Alle connecties gemaakt
    [PCB_Watersysteem.kicad_pcb, PCB_Watersysteem.kicad_sch]
2025-03-07 ground plane fix
    [PCB_Watersysteem.kicad_pcb]
2025-03-08 PCB Update
    samenbrengen designs, polarisaties plaatsen
    [PCB_Watersysteem.kicad_pcb, PCB_Watersysteem.kicad_sch]
2025-03-08 Update PCB
    Logotje toegevoegd
    [PCB_Watersysteem.kicad_pcb]
2025-03-10 Update PCB
    Afmetingen verkleind (100x100), rerouting, clean-up
    [PCB_Watersysteem.kicad_pcb, PCB_Watersysteem.kicad_sch, relays.kicad_sch]
2025-03-10 Update PCB
    Extra eindwerk rond vias en silkscreen
    [PCB_Watersysteem.kicad_pcb]
2025-03-11 Update PCB
    Eindwerk aan PCB (extra vias, meer silkscreen, lichte aanpassing floorplanning,...)
    [PCB_Watersysteem.kicad_pcb, relays.kicad_sch]
2025-03-11 Update PCB: Gerber Files
    Gerber files met drill holes geplot
    [PCB_Watersysteem-B_Cu.gbr, PCB_Watersysteem-B_Mask.gbr, PCB_Watersysteem-B_Paste.gbr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]
2025-03-11 Update PCB
    [PCB_Watersysteem.kicad_pcb]
2025-03-11 Update PCB
    M4 -> M3 in Schema
    [PCB_Watersysteem.kicad_pcb, PCB_Watersysteem.kicad_sch]
2025-03-11 Generated BOM
    [PCB_Watersysteem.csv]
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2025-03-18 Update BOM
    [PCB_Watersysteem.csv]
2025-03-18 files verplaatst
    [Common_Connector.SLDASM, Common_Connector_F_Plate.SLDPRT, Common_Connector_M_Plate.SLDPRT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]
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2025-03-18 Current sensor + fixes
    'GPIO' toegevoegd bij pins, update_interval's geplaatst, power sensing toegevoegd
    [watersysteem.yaml]
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2025-04-02 Weerstandjes gewijzigd voor status LEDs
    [PCB_Watersysteem.kicad_sch]
2025-04-08 hoogtesensoren kallibratie + fixes
    [watersysteem.yaml]
2025-04-13 Changes for uniformity
    [Common_Connector.SLDASM, Common_Connector_F_Plate.SLDPRT, Common_Connector_M_Plate.SLDPRT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]
2025-04-24 Rename Gantt Chart.xlsx to Gantt Chart.xlsx
    [Gantt Chart.xlsx]
2025-04-24 Update and rename Online Gantt 20250218.csv to Online Gantt 20250218.csv
    [Online Gantt 20250218.csv]
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2025-05-06 Upload BOM
    [Bestellijst.xlsx]
2025-05-06 Fixed mistake in BOM
    [Bestellijst.xlsx]
2025-05-07 LED-PCB export files
    [PCB1.GBL, PCB1.GBO, PCB1.GBP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]
2025-05-09 Added driver schematics and PCB
    [Driver.PrjPcb, Driver.SchDoc, ESP32.SchDoc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]
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2025-05-12 Oude log vervangen door planning
    [Gantt Chart.xlsx, Online Gantt 20250218.csv]
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2025-05-12 3D-print pH-houder
    [ProbeHouder - single.stl]
2025-05-12 3D print hoogtesensor
    [HoogtesensorHouder.stl]
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2025-05-13 Add files via upload
    powermeting toevoeging pcb
    [.dxf, powermeting.brd, powermeting.sch]
